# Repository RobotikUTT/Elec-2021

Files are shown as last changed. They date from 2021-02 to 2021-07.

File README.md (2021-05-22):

# Elec-2021
Reprise des cartes électroniques de l'année 2019 cette fois-ci sous Eagle.

TODOS: 
Changer MCP2515 par son modèle en SMD. /Fait

Relier les pins du header CAN. /Fait

Pas de crystal? /Bahsi

Chercher les dimensions du slot de la carte? /Fait

Changer les condos en SMD /...?

3-pin 5V, GND + I2C en plus? /Fait

Changer le R17, R16 en 0207 /Fait

Mettre les IRQ1 et IRQ2 dans le même header GPIO /Fait 

Changer le VDD sur l'Arduino /Fait

Changer le capa d'entrée sur les servos(peut être plus proche au servo) /Fait

Changer les VCC en VDD /..?

Module stepstick? /...?

2-4 de 12V, 6 de GND pins à rajouter /Fait

Relier le 2ème pin du bouton au GND /Fait

Remettre la répétition des résistances pour servos /Fait...?

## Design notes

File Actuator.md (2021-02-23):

-----Components-----

PCA9685:
  - !OE pin: used to enable/disable all LED output at the same time.
    • When low applied to !OE, all outputs enabled (values follow datasheet p.16)
    • When high applied, all outputs follow the value defined by OUTNE[1:0] (p.27)

  - SDA/SCL pins: I2C communication.
    • I2C ADDRESS : 1 + A5 + A4 + A3 + A2 + A1 + A0 + R/W
    • Don't forget the pullups.

  - EXTCLK : External clock, used to synchronize multiple PCA9685 startups.

  - Pins are 5V tolerant

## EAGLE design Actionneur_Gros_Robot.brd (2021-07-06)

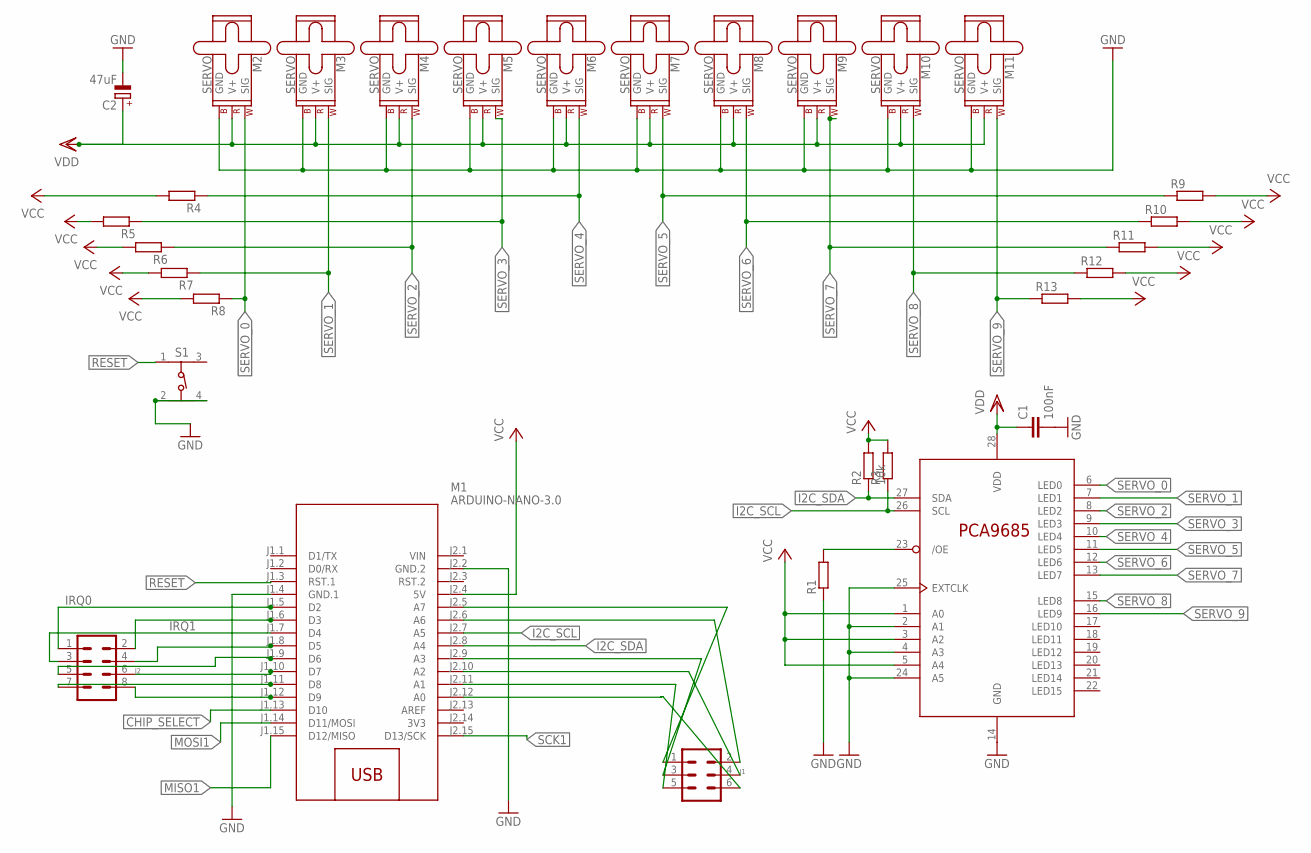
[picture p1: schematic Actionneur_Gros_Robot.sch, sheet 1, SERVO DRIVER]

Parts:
C1: 100nF; C025-025X050
C2: 47uF; E2,5-7
J1: MA03-2
J2: MA04-2
M1: ARDUINO-NANO-3.0
M2, M3, M4, M5, M6, M7, M8, M9, M10, M11: SERVO; 1X03
R1, R3, R4, R5, R6, R7, R8, R9, R10, R11, R12, R13: R-EU_0204/7; 0204/7
R2: 10k; 0204/7
S1: 430182043816
U$1: PCA9685PW; TSSOP28

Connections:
3V3: M1.J2.14 (3V3)
CHIP_SELECT: M1.J1.13 (D10); also elsewhere on the board
GND: C1.2, C2.-, M1.J1.4 (GND.1), M1.J2.2 (GND.2), M2.3 (GND), M3.3 (GND), M4.3 (GND), M5.3 (GND), M6.3 (GND), M7.3 (GND), M8.3 (GND), M9.3 (GND), M10.3 (GND), M11.3 (GND), R1.1, S1.2, S1.4, U$1.2 (A1), U$1.4 (A3), U$1.14 (GND), U$1.24 (A5), U$1.25 (EXTCLK); also elsewhere on the board
I2C_SCL: M1.J2.7 (A5), R3.1, U$1.26 (SCL); also elsewhere on the board
I2C_SDA: M1.J2.8 (A4), R2.1, U$1.27 (SDA); also elsewhere on the board
IRQ0: J2.1, M1.J1.5 (D2)
IRQ1: J2.2, M1.J1.6 (D3)
MISO1: M1.J1.15 (D12/MISO); also elsewhere on the board
MOSI1: M1.J1.14 (D11/MOSI); also elsewhere on the board
unnamed: R1.2, U$1.23 (/OE)
unnamed: J1.6, M1.J2.12 (A0)
unnamed: J1.5, M1.J2.11 (A1)
unnamed: J1.3, M1.J2.9 (A3)
unnamed: J1.4, M1.J2.10 (A2)
unnamed: J1.2, M1.J2.6 (A6)
unnamed: J1.1, M1.J2.5 (A7)
unnamed: J2.8, M1.J1.12 (D9)
unnamed: J2.7, M1.J1.11 (D8)
unnamed: J2.6, M1.J1.10 (D7)
unnamed: J2.5, M1.J1.9 (D6)
unnamed: J2.4, M1.J1.8 (D5)
unnamed: J2.3, M1.J1.7 (D4)
RESET: M1.J1.3 (RST.1), S1.1; also elsewhere on the board
SCK1: M1.J2.15 (D13/SCK); also elsewhere on the board
SERVO_0: M2.1 (SIG), R8.1, U$1.6 (LED0)
SERVO_1: M3.1 (SIG), R7.1, U$1.7 (LED1)
SERVO_2: M4.1 (SIG), R6.1, U$1.8 (LED2)
SERVO_3: M5.1 (SIG), R5.1, U$1.9 (LED3)
SERVO_4: M6.1 (SIG), R4.1, U$1.10 (LED4)
SERVO_5: M7.1 (SIG), R9.1, U$1.11 (LED5)
SERVO_6: M8.1 (SIG), R10.1, U$1.12 (LED6)
SERVO_7: M9.1 (SIG), R11.1, U$1.13 (LED7)
SERVO_8: M10.1 (SIG), R12.1, U$1.15 (LED8)
SERVO_9: M11.1 (SIG), R13.1, U$1.16 (LED9)
VCC: C1.1, M1.J2.4 (5V), R2.2, R3.2, R4.2, R5.2, R6.2, R7.2, R8.2, R9.2, R10.2, R11.2, R12.2, R13.2, U$1.1 (A0), U$1.3 (A2), U$1.5 (A4), U$1.28 (VDD); also elsewhere on the board
VDD: C2.+, M2.2 (V+), M3.2 (V+), M4.2 (V+), M5.2 (V+), M6.2 (V+), M7.2 (V+), M8.2 (V+), M9.2 (V+), M10.2 (V+), M11.2 (V+); also elsewhere on the board
VIN: M1.J2.1 (VIN)

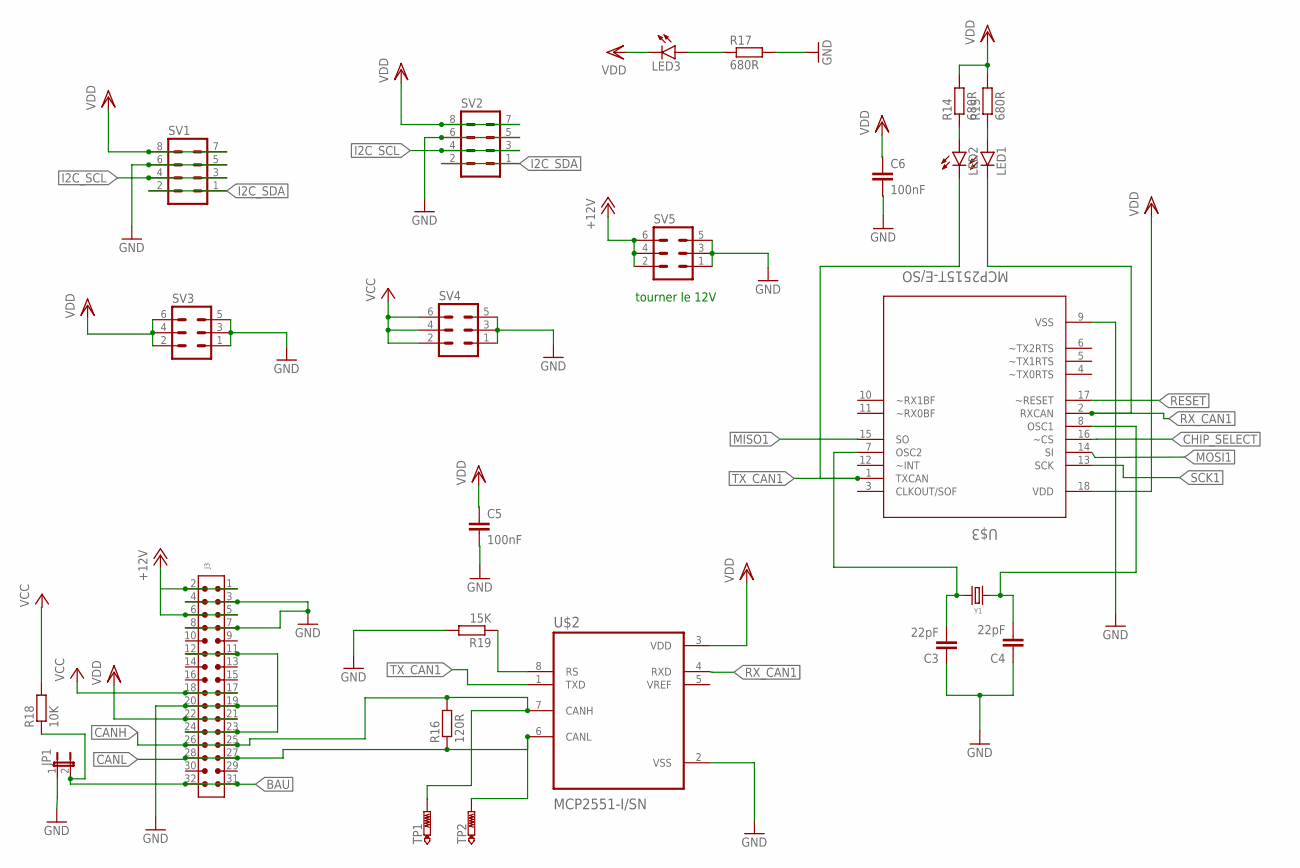
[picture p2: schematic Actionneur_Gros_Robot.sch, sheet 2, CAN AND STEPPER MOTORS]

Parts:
C3, C4: 22pF; C025-025X050
C5, C6: 100nF; C025-025X050
J3: 6130XX21021_61303221021; 61303221021
JP1: JP1E; JP1
LED1, LED2, LED3: LED3MM
R14, R15: 680R; 0207/10
R16: 120R; 0207/7
R17: 680R; 0207/7
R18: 10K; 0207/7
R19: 15K; 0207/7
SV1, SV2: MA04-2
SV3, SV4, SV5: MA03-2
TP1, TP2: PTR1PAD1-17; P1-17
U$2: MCP2551-I/SN; SOIC127P599X175-8N
U$3: MCP2515T-E/SO; SOIC127P1030X265-18N
Y1: 16MHz; HC49UP

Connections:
+12V: J3.1, J3.2, SV5.2, SV5.4, SV5.6
BAU: J3.31, J3.32, JP1.2, R18.1
CANH: J3.25, J3.26, R16.2, TP1.TP, U$2.7 (CANH)
CANL: J3.27, J3.28, R16.1, TP2.TP, U$2.6 (CANL)
CHIP_SELECT: U$3.16 (~CS); also elsewhere on the board
GND: C3.1, C4.1, C5.2, C6.2, J3.3, J3.4, J3.7, J3.8, J3.11, J3.12, J3.19, J3.20, J3.23, J3.24, JP1.1, R17.2, R19.2, SV1.5, SV1.6, SV2.5, SV2.6, SV3.1, SV3.3, SV3.5, SV4.1, SV4.3, SV4.5, SV5.1, SV5.3, SV5.5, U$2.2 (VSS), U$3.9 (VSS); also elsewhere on the board
I2C_SCL: SV1.3, SV1.4, SV2.3, SV2.4; also elsewhere on the board
I2C_SDA: SV1.1, SV1.2, SV2.1, SV2.2; also elsewhere on the board
MISO1: U$3.15 (SO); also elsewhere on the board
MOSI1: U$3.14 (SI); also elsewhere on the board
unnamed: J3.5, J3.6
unnamed: R19.1, U$2.8 (RS)
unnamed: LED1.A, R15.1
unnamed: LED2.A, R14.1
unnamed: LED3.A, R17.1
unnamed: C4.2, U$3.8 (OSC1), Y1.1
unnamed: C3.2, U$3.7 (OSC2), Y1.2
RESET: U$3.17 (~RESET); also elsewhere on the board
RX_CAN1: LED1.K (C), U$2.4 (RXD), U$3.2 (RXCAN)
SCK1: U$3.13 (SCK); also elsewhere on the board
TX_CAN1: LED2.K (C), U$2.1 (TXD), U$3.1 (TXCAN)
VCC: J3.17, J3.18, R18.2, SV4.2, SV4.4, SV4.6; also elsewhere on the board
VDD: C5.1, C6.1, J3.21, J3.22, LED3.K (C), R14.2, R15.2, SV1.7, SV1.8, SV2.7, SV2.8, SV3.2, SV3.4, SV3.6, U$2.3 (VDD), U$3.18 (VDD); also elsewhere on the board

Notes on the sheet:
tourner le 12V

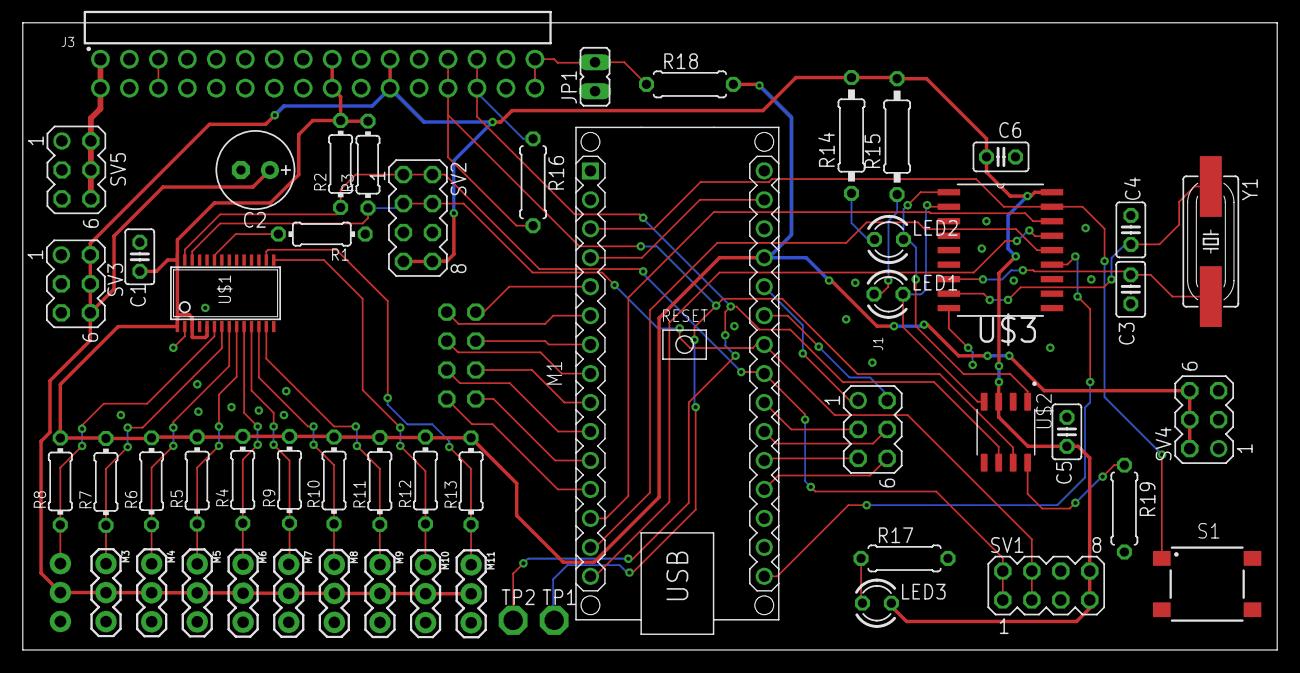
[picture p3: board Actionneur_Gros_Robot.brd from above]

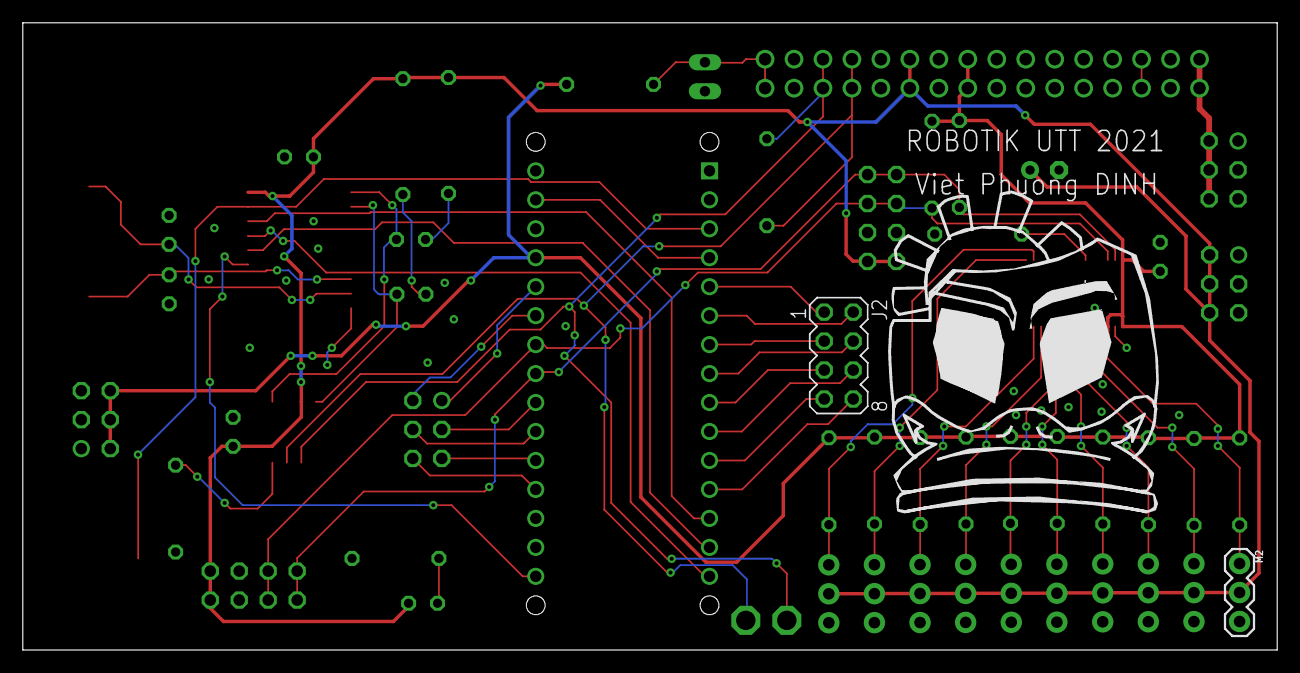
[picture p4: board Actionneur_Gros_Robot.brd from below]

Board: 2 copper layers, 110.0 x 55.0 mm, 55 parts (2 on the bottom side), 48 nets.

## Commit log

2021-02-23 Needed librairies for CAD models added. Mainframe actuators schematics available.
    [Actionneur_Gros_Robot.sch]
2021-03-25 added MCP2551 and MCP 2515
    [Actionneur_Gros_Robot.sch]
2021-05-11 Routing in progress
    [Actionneur_Gros_Robot.brd, Actionneur_Gros_Robot.sch]
2021-05-11 En attente de révision
    [Actionneur_Gros_Robot.brd]
2021-05-22 v2 en cours de révision
    [Actionneur_Gros_Robot.brd, Actionneur_Gros_Robot.sch]
2021-05-22 Ajout des pins 12V
    [Actionneur_Gros_Robot.brd, Actionneur_Gros_Robot.sch]
2021-06-08 chgt schéma bouton d'arrêt d'urgence, condo 10 uF sur VDD
    [Actionneur_Gros_Robot.brd, Actionneur_Gros_Robot.sch]
2021-06-10 Added CAM job
    [Actionneur_Gros_Robot.brd, Actionneur_Gros_Robot.sch]
2021-06-16 ajout des fichiers gerber
    [Actionneur_Gros_Robot.brd]
2021-07-06 Added testpins for CANH and CANL
    [Actionneur_Gros_Robot.brd, Actionneur_Gros_Robot.sch]

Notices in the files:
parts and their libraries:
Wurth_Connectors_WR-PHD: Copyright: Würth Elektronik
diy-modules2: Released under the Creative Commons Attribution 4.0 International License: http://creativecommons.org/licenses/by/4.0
